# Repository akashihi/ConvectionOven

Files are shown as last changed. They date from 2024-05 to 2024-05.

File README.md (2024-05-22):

<!-- Improved compatibility of back to top link: See: https://github.com/othneildrew/Best-README-Template/pull/73 -->

<h3 align="center">Adler Ad 6304 Convection Oven controller board</h3>
<div>
  <p align="center">
    Modern replacement for the Adler Ad 6304 control circuit. 
    <br />
    <a href="https://github.com/akashihi/ConvectionOven"><strong>Explore the docs »</strong></a>
    <br />
    <br />
  </p>
</div>

<!-- TABLE OF CONTENTS -->
<details>
  <summary>Table of Contents</summary>
  <ol>
    <li>
      <a href="#about-the-project">About The Project</a>
    </li>
    <li>
      <a href="#getting-started">Getting Started</a>
      <ul>
        <li><a href="#housing">Housing</a></li>
        <li><a href="#controls">Controls</a></li>
        <li><a href="#hall-sensor">Hall sensor</a></li>
        <li><a href="#pcb">PCB</a></li>
        <li><a href="#firmware">Firmware</a></li>
      </ul>
    </li>
    <li><a href="#usage">Usage</a></li>
    <li><a href="#roadmap">Roadmap</a></li>
    <li><a href="#contributing">Contributing</a></li>
    <li><a href="#license">License</a></li>
    <li><a href="#contact">Contact</a></li>
  </ol>
</details>

<!-- ABOUT THE PROJECT -->
## About The Project

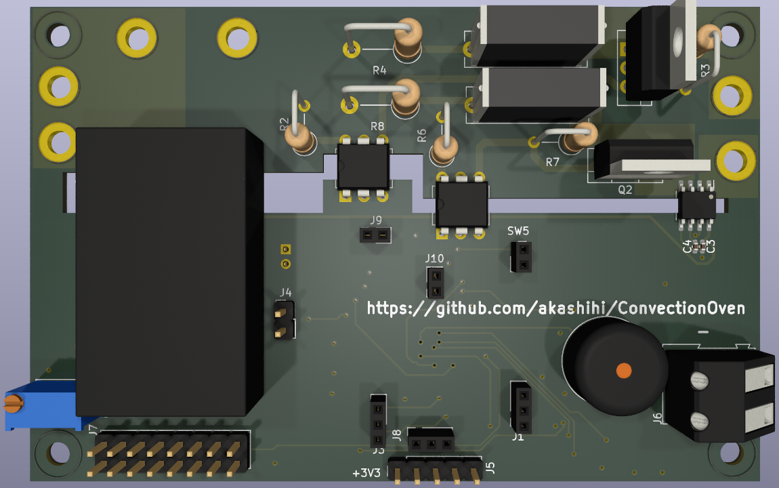
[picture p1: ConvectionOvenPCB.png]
Product Name Screen Shot


This is a drop-in replacement of an analog control circuit of the Adler Ad 6304 oven.

The updated control circuit provides the following improvements to the original circuit:

* Easily cancellable timer
* Magnetic handle position sensor
* PID temperature control
* LCD user interface
* Overheat protection
* Motor protection (currently disabled in firmware)
* Sleeping mode (currently disabled)

<p align="right">(<a href="#readme-top">back to top</a>)</p>

<!-- GETTING STARTED -->
## Getting Started

Get an Adler Ad 6304 oven that you would like to upgrade. Broken oven is fine too, 
in case heater element and motor are still working. You will need to completely disassemble
the oven and remove most of it. However, some elements will be reused:

* Heater and heater wires
* Motor and motor wires
* Thermistor. It is hidden in the white braid and mounted directly to the upper fan housing. 
Leave it as it is or move closer to the power outlet.

Everything else, including the plastic enclosure, could be thrown to the trash :D 

### Housing

Housing consists of five 3D printable parts:

* Inner and outer axles
* Upper and lower handle parts
* The actual electronics housing

Both axles and handle parts are easy to print. The housing is more tricky, as you need 
supports only for the bigger overhands, like encoders insets or cut for a handle. 
You *do not* need supports for the ventilation cuts. Putting supports there will make your life
much harder, as those supports are almost impossible to remove.

While assembling the housing, you need to put inner axles through the housing and glue them
to the outer axles, so they will become a real axle. For the handle you'll need some M3 bolts
and nuts. Additionally, you need to put several strong 6mmx3mm magnets into the magnet
pocket of the lower handle.

After assembling the handle, put the M3 insets into the hall sensor PCB mounting holes,
screen mounting holes and the main PCB mounting holes.

As the last step, mount the IEC 60320 C14 connector to the respective slot on the housing side.

<p align="right">(<a href="#readme-top">back to top</a>)</p>

### Controls

All controls are mounted to the housing. You will need to mount:

* Two encoders, one for the temperature setting, one for the timer setting
* Two buttons. One for the sleep mode (unused atm), one to switch the cooking mode on and off
* Two LEDs, one shows whether oven is cooking or not, another one shows the heater state
* 16x2 HD44780 screen with 3.3V support. The 5V screens will not work in this design.

<p align="right">(<a href="#readme-top">back to top</a>)</p>

### Hall sensor

Hall sensor is mounted on a separate PCB under the handle. This design uses omni-polar
hall sensor with an open-drain output.

<p align="right">(<a href="#readme-top">back to top</a>)</p>

### PCB

Control PCB is a four layer PCB, split into hot side and cold side. Follow the schematics
and PCB design for the assembly. Additional guidance:

* The U3 IC is required, as it closes the motor control circuit. However, it is not
used in the firmware, so rest of the components (C3, C4, R11, R12, D1, C20) could be omitted for now.
* You can skip the U4 IC and related components (R10, C11, C6, C5)
* You need to short circuit R25, as there is no sleep mode implemented yet
* TRIACs Q1 and Q2 *require* heatsinks
* You may test the cold side of the circuit by injecting power (+5V) directly to the J4

Assembled PCB should be put into the housing and connected to the controls, power socket, heater and
motor. Please connect motor to the control channel equipped with a current sensor. It
is recommended to have a fuse between the power socket and the control PCB. Same way
connect the thermistor, mentioned above, in series with the fuse.

<p align="right">(<a href="#readme-top">back to top</a>)</p>

### Firmware

Precompiled firmware is provided in the `fw.bin` file. 

The firmware is written in Rust and could be compiled with the following commands:

```shell
cargo build --release
cargo objcopy --release --bin fw -- -O binary fw.bin
```

You can upload the firmware with a `st-flash` tool:

```shell
st-flash erase 
st-flash write fw.hex 0x8000000
st-flash reset
```

The oven should start immediately after reset

<p align="right">(<a href="#readme-top">back to top</a>)</p>

## Usage

To start cooking you have to set a timer (up to 3 hours) and desired temperature (up to 250 degrees),
lower the handle and press cooking button. The oven will start immediately.

Raising the handle or pressing the cooking button stops the motor and heater instantly.

You can adjust the timer and desired temperature during the cooking. In one minute before
the timer expiration you will get a short beep accompanied by a longer beep after timer
expiration.

After cooking please immediately open the oven and put a top lid on the lid rack to 
avoid circuit overheat.  

<p align="right">(<a href="#readme-top">back to top</a>)</p>

<!-- ROADMAP -->
## Roadmap

- [ ] Implement sleep mode
- [ ] Implement motor protection

<p align="right">(<a href="#readme-top">back to top</a>)</p>

<!-- CONTRIBUTING -->
## Contributing

Contributions are what make the open source community such an amazing place to learn, inspire, and create. Any contributions you make are **greatly appreciated**.

If you have a suggestion that would make this better, please fork the repo and create a pull request.

1. Fork the Project
2. Create your Feature Branch (`git checkout -b feature/AmazingFeature`)
3. Commit your Changes (`git commit -m 'Add some AmazingFeature'`)
4. Push to the Branch (`git push origin feature/AmazingFeature`)
5. Open a Pull Request

<p align="right">(<a href="#readme-top">back to top</a>)</p>

<!-- LICENSE -->
## License

Distributed under the GPLv3 License. See `LICENSE.txt` for more information.

<p align="right">(<a href="#readme-top">back to top</a>)</p>

<!-- CONTACT -->
## Contact

Denis Chaplygin - @akashihi@mathstodon.xyz - akashihi@gmail.com

Project Link: [https://github.com/akashihi/ConvectionOven](https://github.com/github_username/repo_name)

<p align="right">(<a href="#readme-top">back to top</a>)</p>

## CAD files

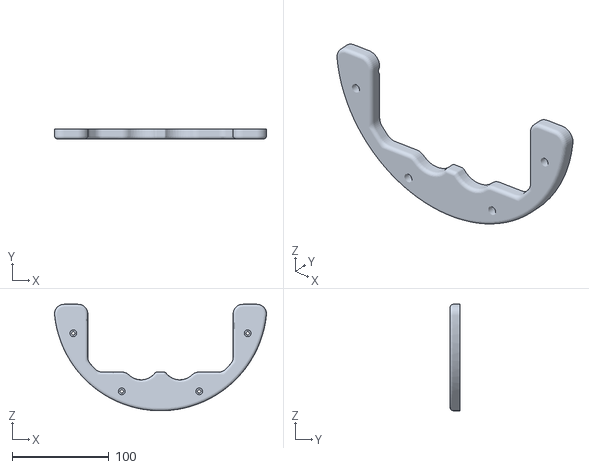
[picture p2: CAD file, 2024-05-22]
Housing/UpperHandle.STL
219.0 x 10.00 x 110.0

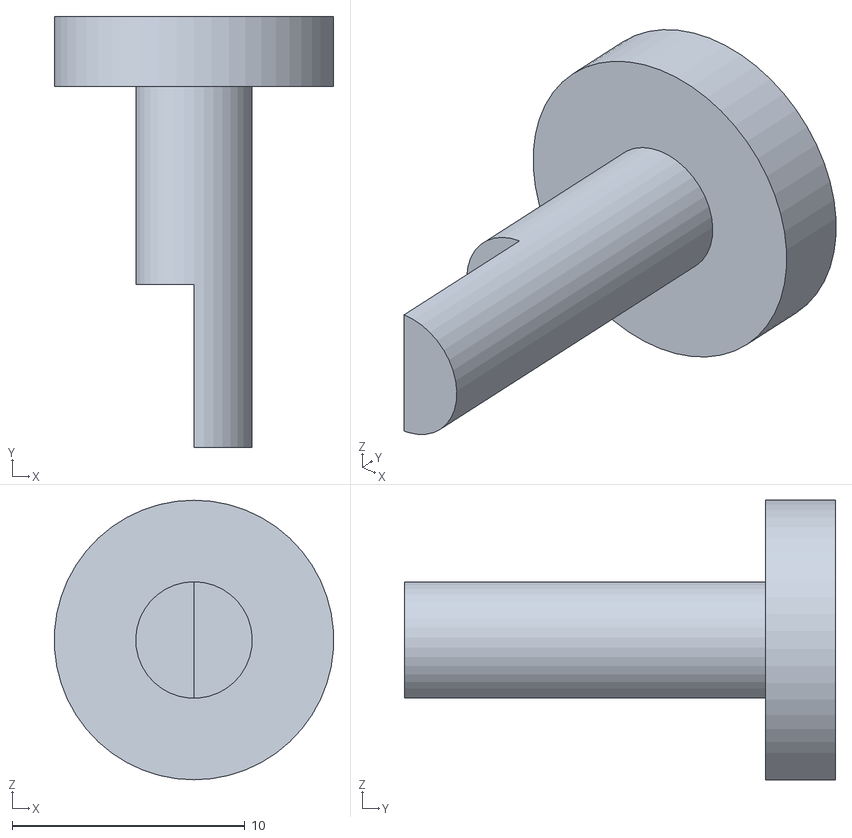
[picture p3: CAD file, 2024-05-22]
Housing/InnerAxle.STL
12.0 x 18.5 x 12.0

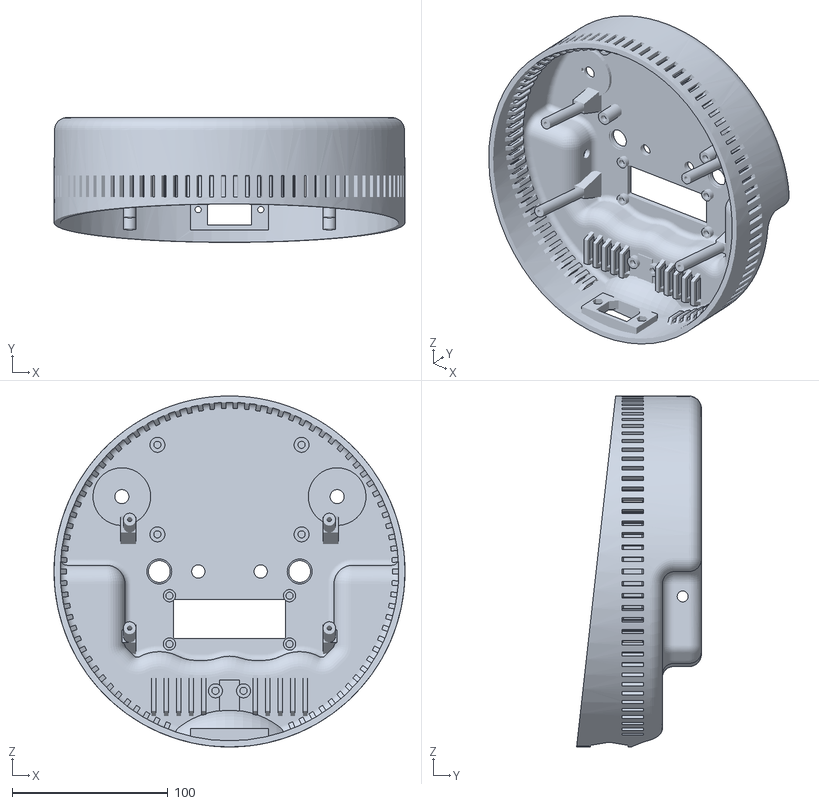
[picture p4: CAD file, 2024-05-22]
Housing/Cover.STL
225.0 x 80.0 x 225.0

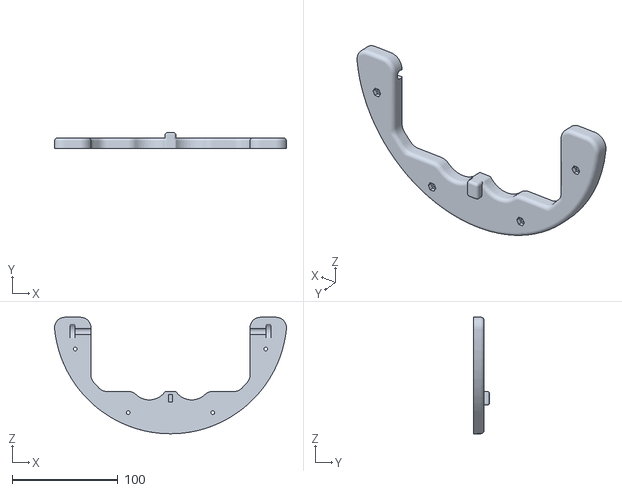
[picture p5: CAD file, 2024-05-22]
Housing/LowerHandle.STL
219.0 x 15.0 x 110.0

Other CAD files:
Housing/OuterAxle.STL

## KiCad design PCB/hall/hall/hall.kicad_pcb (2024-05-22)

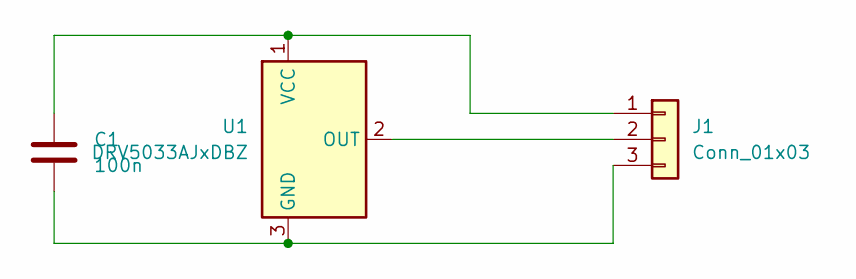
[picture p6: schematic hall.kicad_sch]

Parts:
C1: 100n; C_0603_1608Metric
J1: Conn_01x03; PinHeader_1x03_P2.00mm_Vertical
U1: DRV5033AJxDBZ; SOT-23

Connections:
unnamed: C1.1, J1.1, U1.1 (VCC)
unnamed: J1.2, U1.2 (OUT)
unnamed: C1.2, J1.3, U1.3 (GND)

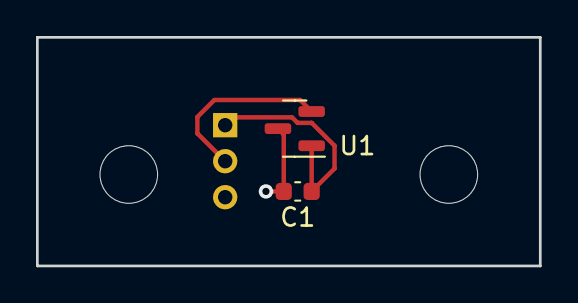
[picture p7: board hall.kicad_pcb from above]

Board: 2 copper layers, 27.9 x 12.7 mm, 3 parts (1 on the bottom side), 3 nets.

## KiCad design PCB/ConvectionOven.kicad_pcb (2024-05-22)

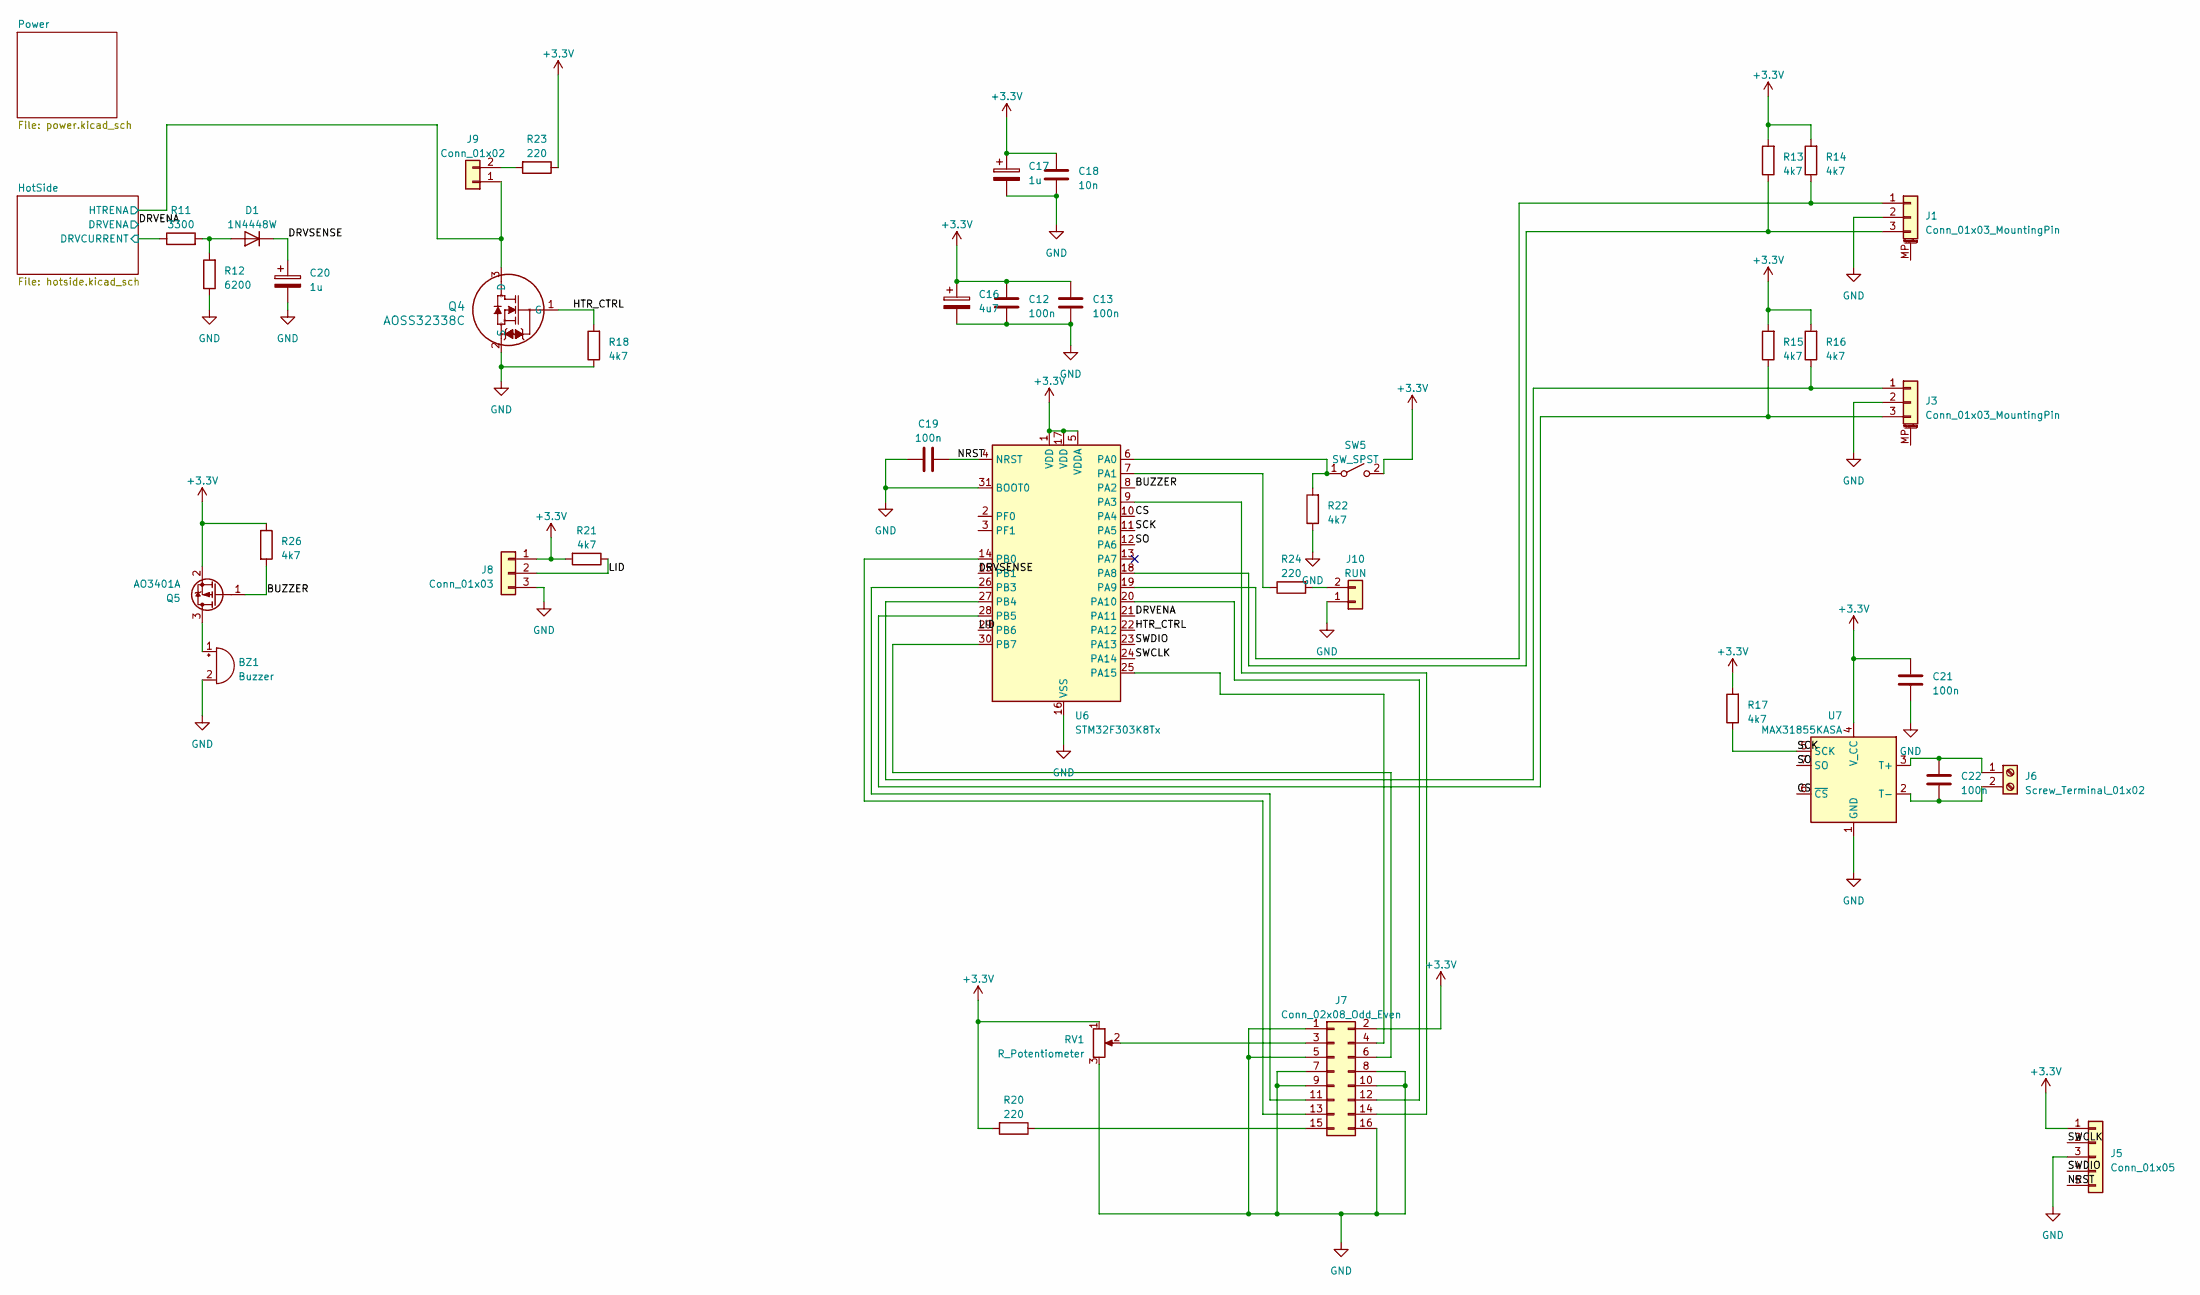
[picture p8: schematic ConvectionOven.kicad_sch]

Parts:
BZ1: Buzzer; Buzzer_12x9.5RM7.6
C12, C13, C19, C21, C22: 100n; C_0402_1005Metric_Pad0.74x0.62mm_HandSolder
C16: 4u7; C_Elec_4x5.4
C17, C20: 1u; C_0805_2012Metric_Pad1.18x1.45mm_HandSolder
C18: 10n; C_0805_2012Metric_Pad1.18x1.45mm_HandSolder
D1: 1N4448W; D_SOD-123
J1, J3: Conn_01x03_MountingPin; PinSocket_1x03_P2.00mm_Vertical
J5: Conn_01x05; PinHeader_1x05_P2.54mm_Vertical
J6: Screw_Terminal_01x02; TerminalBlock_Altech_AK300-2_P5.00mm
J7: Conn_02x08_Odd_Even; PinHeader_2x08_P2.54mm_Vertical
J8: Conn_01x03; PinSocket_1x03_P2.00mm_Vertical
J9: Conn_01x02; PinSocket_1x02_P2.00mm_Vertical
J10: RUN; PinSocket_1x02_P2.00mm_Vertical
Q4: AOSS32338C; SOT-23-3
Q5: AO3401A; SOT-23
R11: 3300; R_0805_2012Metric_Pad1.20x1.40mm_HandSolder
R12: 6200; R_1206_3216Metric_Pad1.30x1.75mm_HandSolder
R13, R14, R15, R16, R17, R18, R21, R22, R26: 4k7; R_0805_2012Metric_Pad1.20x1.40mm_HandSolder
R20, R23, R24: 220; R_0805_2012Metric_Pad1.20x1.40mm_HandSolder
RV1: R_Potentiometer; Potentiometer_Bourns_3296W_Vertical
SW5: SW_SPST; PinSocket_1x02_P2.00mm_Vertical
U6: STM32F303K8Tx; LQFP-32_7x7mm_P0.8mm
U7: MAX31855KASA; SOIC-8_3.9x4.9mm_P1.27mm

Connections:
+3.3V: C12.1, C13.1, C16.1, C17.1, C18.1, C21.1, J5.1, J7.2, J8.1, Q5.2 (S), R13.2, R14.2, R15.2, R16.2, R17.2, R20.2, R21.2, R23.1, R26.1, RV1.1, SW5.2 (B), U6.1 (VDD), U6.5 (VDDA), U6.17 (VDD), U7.4 (V_CC); also elsewhere on the board
/BUZZER: Q5.1 (G), R26.2, U6.8 (PA2)
/CS: U6.10 (PA4), U7.6 (~CS)
/DRVENA: U6.21 (PA11); also elsewhere on the board
/DRVSENSE: C20.1, D1.1 (K), U6.15 (PB1)
/HTR_CTRL: Q4.1 (G), R18.2, U6.22 (PA12)
/HotSide/DRVCURRENT: R11.1; also elsewhere on the board
/HotSide/HTRENA: J9.1, Q4.3 (D); also elsewhere on the board
/LID: J8.2, R21.1, U6.29 (PB6)
/NRST: C19.2, J5.5, U6.4 (NRST)
/SCK: R17.1, U6.11 (PA5), U7.5 (SCK)
/SO: U6.12 (PA6), U7.7 (SO)
/SWCLK: J5.2, U6.24 (PA14)
/SWDIO: J5.4, U6.23 (PA13)
GND: BZ1.2 (+), C12.2, C13.2, C16.2, C17.2, C18.2, C19.1, C20.2, C21.2, J1.2, J3.2, J5.3, J7.1, J7.5, J7.7, J7.8, J7.9, J7.10, J7.16, J8.3, J10.1, Q4.2 (S), R12.1, R18.1, R22.1, RV1.3, U6.16 (VSS), U6.31 (BOOT0), U6.32 (VSS), U7.1 (GND); also elsewhere on the board
unnamed: BZ1.1 (-), Q5.3 (D)
unnamed: D1.2 (A), R11.2, R12.2
unnamed: J1.1, R14.1, U6.19 (PA9)
unnamed: J1.3, R13.1, U6.18 (PA8)
unnamed: J3.1, R16.1, U6.27 (PB4)
unnamed: J3.3, R15.1, U6.28 (PB5)
unnamed: C22.1, J6.1, U7.3 (T+)
unnamed: C22.2, J6.2, U7.2 (T-)
unnamed: J7.3, RV1.2
unnamed: J7.4, U6.25 (PA15)
unnamed: J7.6, U6.30 (PB7)
unnamed: J7.11, U6.26 (PB3)
unnamed: J7.12, U6.20 (PA10)
unnamed: J7.13, U6.14 (PB0)
unnamed: J7.14, U6.9 (PA3)
unnamed: J7.15, R20.1
unnamed: J9.2, R23.2
unnamed: J10.2, R24.2
unnamed: R22.2, SW5.1 (A), U6.6 (PA0)
unnamed: R24.1, U6.7 (PA1)

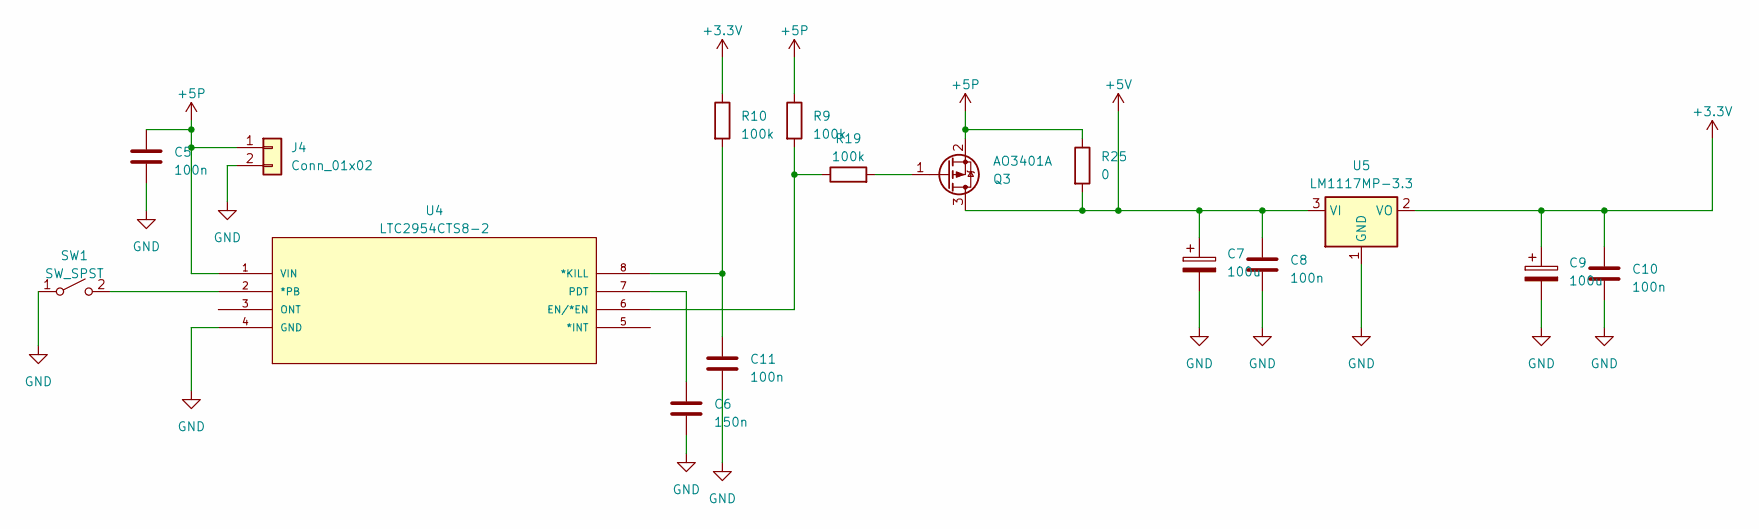
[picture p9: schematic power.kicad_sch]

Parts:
C5, C8, C10, C11: 100n; C_0402_1005Metric_Pad0.74x0.62mm_HandSolder
C6: 150n; C_0402_1005Metric_Pad0.74x0.62mm_HandSolder
C7, C9: 100u; CP_EIA-7343-15_Kemet-W_Pad2.25x2.55mm_HandSolder
J4: Conn_01x02; PinHeader_1x02_P2.54mm_Vertical
Q3: AO3401A; SOT-23
R9, R19: 100k; R_0805_2012Metric_Pad1.20x1.40mm_HandSolder
R10: 100k; R_0603_1608Metric_Pad0.98x0.95mm_HandSolder
R25: 0; R_0805_2012Metric_Pad1.20x1.40mm_HandSolder
SW1: SW_SPST; PinSocket_1x02_P2.00mm_Vertical
U4: LTC2954CTS8-2; TSOT-23-8_HandSoldering; MANUFACTURER_PART_NUMBER ltc2954cts82
U5: LM1117MP-3.3; SOT-223-3_TabPin2

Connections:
+3.3V: C9.1, C10.1, R10.1, U5.2 (VO); also elsewhere on the board
+5P: C5.1, J4.1, Q3.2 (S), R9.1, R25.1, U4.1 (VIN); also elsewhere on the board
+5V: C7.1, C8.1, Q3.3 (D), R25.2, U5.3 (VI); also elsewhere on the board
GND: C5.2, C6.2, C7.2, C8.2, C9.2, C10.2, C11.2, J4.2, SW1.1 (A), U4.4 (GND), U5.1 (GND); also elsewhere on the board
unnamed: Q3.1 (G), R19.2
unnamed: SW1.2 (B), U4.2 (*PB)
unnamed: C11.1, R10.2, U4.8 (*KILL)
unnamed: R9.2, R19.1, U4.6 (EN/*EN)
unnamed: C6.1, U4.7 (PDT)

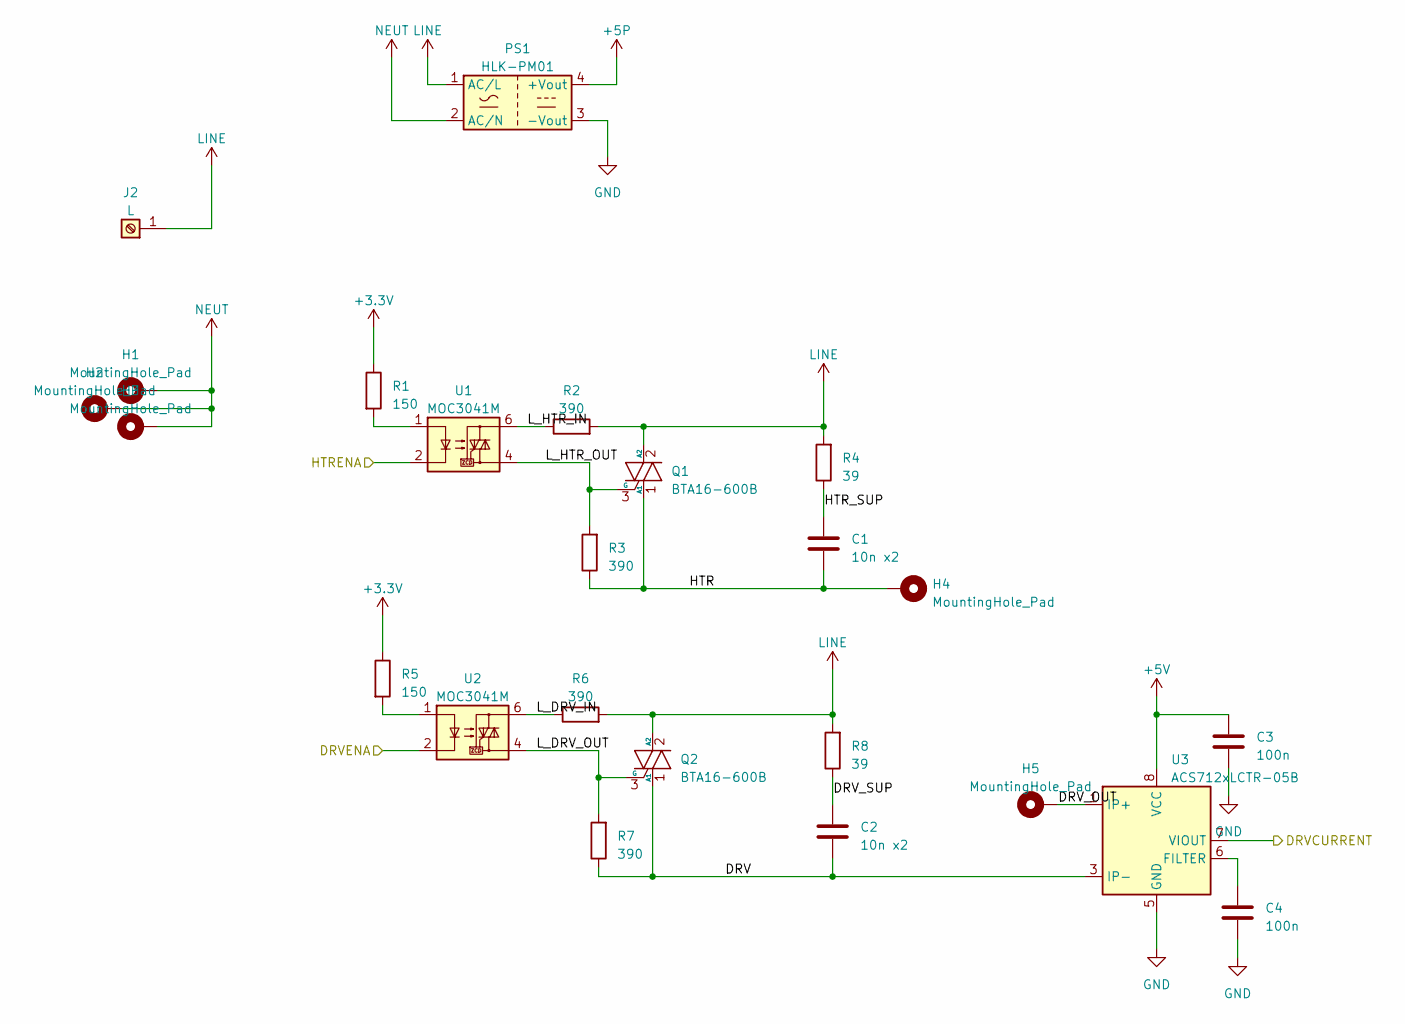
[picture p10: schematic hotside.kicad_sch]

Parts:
C1, C2: 10n x2; C_Rect_L16.5mm_W4.7mm_P15.00mm_MKT
C3, C4: 100n; C_0402_1005Metric_Pad0.74x0.62mm_HandSolder
H1, H2, H3, H4, H5: MountingHole_Pad; MountingHole_3.2mm_M3_DIN965_Pad_TopBottom
J2: L; MountingHole_3.2mm_M3_DIN965_Pad_TopBottom
PS1: HLK-PM01; Converter_ACDC_HiLink_HLK-PMxx
Q1, Q2: BTA16-600B; TO-220-3_Vertical
R1, R5: 150; R_0603_1608Metric_Pad0.98x0.95mm_HandSolder
R2, R3, R6, R7: 390; R_Axial_DIN0309_L9.0mm_D3.2mm_P5.08mm_Vertical
R4, R8: 39; R_Axial_DIN0411_L9.9mm_D3.6mm_P7.62mm_Vertical
U1, U2: MOC3041M; DIP-6_W7.62mm
U3: ACS712xLCTR-05B; SOIC-8_3.9x4.9mm_P1.27mm

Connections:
+3.3V: R1.1, R5.1; also elsewhere on the board
+5P: PS1.4 (+Vout); also elsewhere on the board
+5V: C3.1, U3.8 (VCC); also elsewhere on the board
/DRVENA: U2.2; also elsewhere on the board
/HotSide/DRV: C2.2, Q2.1 (A1), R7.1, U3.3 (IP-), U3.4 (IP-)
/HotSide/DRVCURRENT: U3.7 (VIOUT); also elsewhere on the board
/HotSide/DRV_OUT: H5.1, U3.1 (IP+), U3.2 (IP+)
/HotSide/DRV_SUP: C2.1, R8.1
/HotSide/HTR: C1.2, H4.1, Q1.1 (A1), R3.1
/HotSide/HTRENA: U1.2; also elsewhere on the board
/HotSide/HTR_SUP: C1.1, R4.1
/HotSide/L_DRV_IN: R6.1, U2.6
/HotSide/L_DRV_OUT: Q2.3 (G), R7.2, U2.4
/HotSide/L_HTR_IN: R2.1, U1.6
/HotSide/L_HTR_OUT: Q1.3 (G), R3.2, U1.4
GND: C3.2, C4.2, PS1.3 (-Vout), U3.5 (GND); also elsewhere on the board
LINE: J2.1, PS1.1 (AC/L), Q1.2 (A2), Q2.2 (A2), R2.2, R4.2, R6.2, R8.2
NEUT: H1.1, H2.1, H3.1, PS1.2 (AC/N)
unnamed: R1.2, U1.1
unnamed: R5.2, U2.1
unnamed: C4.1, U3.6 (FILTER)

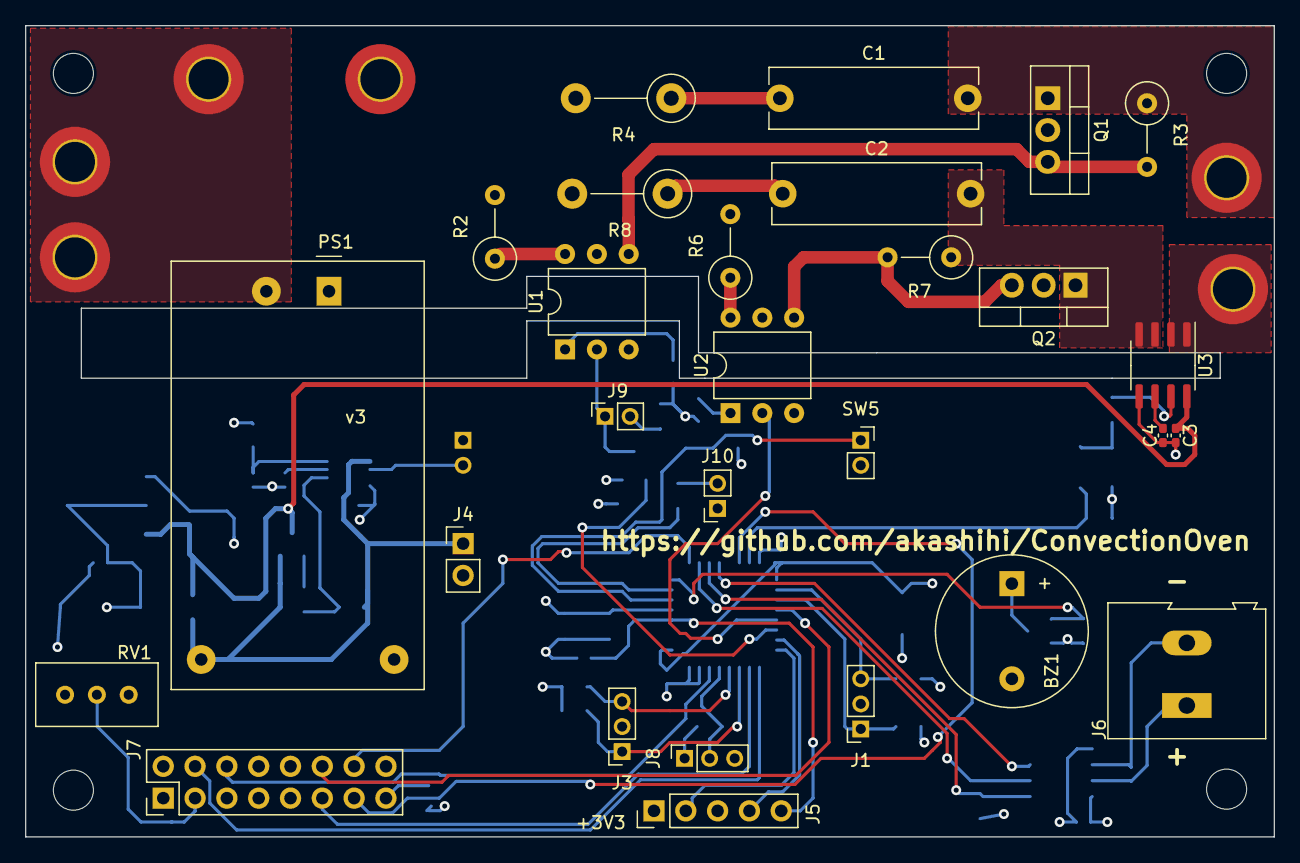
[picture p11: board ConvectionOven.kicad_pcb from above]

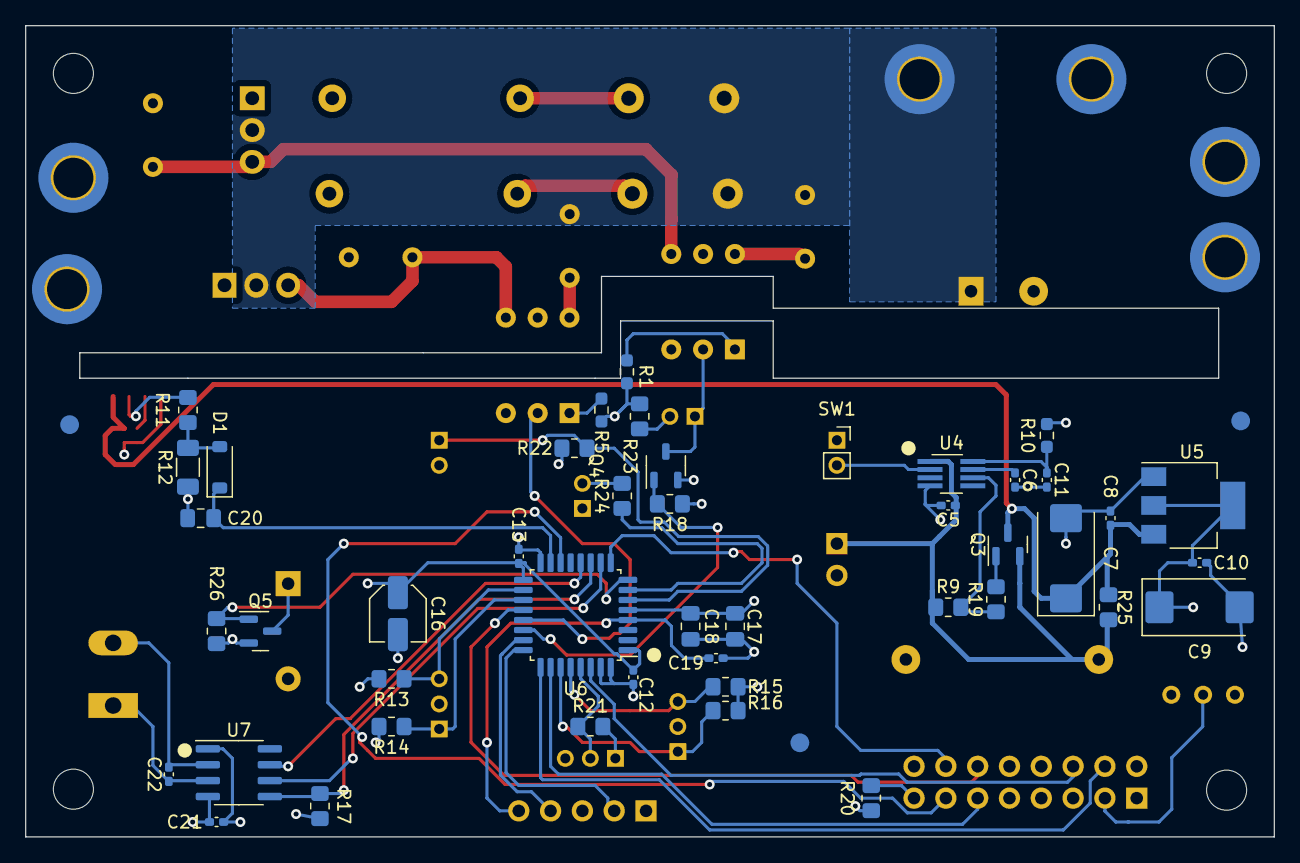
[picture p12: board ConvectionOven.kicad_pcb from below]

Board: 4 copper layers, 99.7 x 64.8 mm, 79 parts (45 on the bottom side), 56 nets.

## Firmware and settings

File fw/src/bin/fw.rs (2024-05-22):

#![no_main]
#![no_std]

extern crate panic_halt;

use fw as _;

#[rtic::app(device = stm32f3xx_hal::pac, dispatchers = [FMC])]
mod app {
    use cortex_m::peripheral::NVIC;
    use stm32f3xx_hal::prelude::*;
    use dwt_systick_monotonic::DwtSystick;
    use stm32f3xx_hal::gpio::Edge;
    use stm32f3xx_hal::timer::{Timer, Event};
    use stm32f3xx_hal::adc;
    use fw::board::{Board, CookBtn, Lid};
    use fw::encoder::{EncoderReaderTIM1, EncoderReaderTIM3};
    use dwt_systick_monotonic::ExtU32;
    use stm32f3xx_hal::adc::{VoltageInternalReference};
    use stm32f3xx_hal::pac::{TIM2, TIM6, TIM15};
    use fw::buzzer::BuzzerManager;
    use fw::current_sensor::{CurrentReader, CurrentSensor};
    use fw::delay::TimDelay;
    use fw::display::LcdDisplay;
    use fw::state::manager::StateManager;
    use fw::state::OvenControlHardware;
    use fw::temp_sensor::TempSensor;

    #[monotonic(binds = SysTick, default = true)]
    type SysMono = DwtSystick<64_000_000>;

    #[shared]
    struct Shared {
        cook_btn_debounce: bool,
        lid_debounce: bool,
        lid: Lid,
        state: StateManager,
    }

    #[local]
    struct Local {
        cook_btn: CookBtn,
        current_timer: Timer<TIM2>,
        current_reader: CurrentReader,
        state_poll_timer: Timer<TIM6>,
        pid_timer: Timer<TIM15>
    }

    #[init]
    fn init(mut cx: init::Context) -> (Shared, Local, init::Monotonics) {
        //Set up the system clock
        let mut rcc = cx.device.RCC.constrain();
        let mut flash = cx.device.FLASH.constrain();
        let clocks = rcc.cfgr.sysclk(64.MHz()).freeze(&mut flash.acr);
        let mut syscfg = cx.device.SYSCFG.constrain(&mut rcc.apb2);
        let mut exti = cx.device.EXTI;

        //Set up monotonic timer
        cx.core.DCB.enable_trace();
        cx.core.DWT.enable_cycle_counter();
        let mono = DwtSystick::new(&mut cx.core.DCB, cx.core.DWT, cx.core.SYST, clocks.hclk().0);

        //Configure TIM7 as a delay provider
        let mut delay = TimDelay::new(cx.device.TIM7, clocks, &mut rcc.apb1);

        //Configure board
        let mut board = Board::new(cx.device.GPIOA, cx.device.GPIOB, cx.device.SPI1, &mut rcc.ahb, &mut rcc.apb2, clocks, &mut delay);

        //Setup event timers
        let mut state_poll_timer = Timer::new(cx.device.TIM6, clocks, &mut rcc.apb1);
        state_poll_timer.start(100.milliseconds());
        state_poll_timer.enable_interrupt(Event::Update);
        let mut pid_timer = Timer::new(cx.device.TIM15, clocks, &mut rcc.apb2);
        pid_timer.start(10.seconds());
        pid_timer.enable_interrupt(Event::Update);

        //Configure temperature encoder
        let tim1 = Timer::new(cx.device.TIM1, clocks, &mut rcc.apb2);
        let temp_encoder = EncoderReaderTIM1::new(tim1.free(), 10, 50);

        //Configure time encoder
        let tim3 = Timer::new(cx.device.TIM3, clocks, &mut rcc.apb1);
        let time_encoder = EncoderReaderTIM3::new(tim3.free(), 0, 180);

        //Configure drive current sensor
        let mut current_timer = Timer::new(cx.device.TIM2, clocks, &mut rcc.apb1);
        current_timer.start(10.milliseconds());
        current_timer.enable_interrupt(Event::Update);
        let mut adc_common_current = adc::CommonAdc::new(cx.device.ADC1_2, &clocks, &mut rcc.ahb);
        let mut adc_pair_current = (cx.device.ADC1, cx.device.ADC2);
        let v_in = VoltageInternalReference::new(&mut adc_common_current, &mut adc_pair_current);
        let adc_current = adc::Adc::new(adc_pair_current.0, adc::config::Config::default(), &clocks, &adc_common_current).into_oneshot();

        //Configure the interrrupts
        syscfg.select_exti_interrupt_source(&board.cook_btn);
        board.cook_btn.trigger_on_edge(&mut exti, Edge::Rising);
        board.cook_btn.enable_interrupt(&mut exti);
        syscfg.select_exti_interrupt_source(&board.lid);
        board.lid.trigger_on_edge(&mut exti, Edge::Falling);
        board.lid.enable_interrupt(&mut exti);

        unsafe {
            NVIC::unmask(board.cook_btn.interrupt());
            NVIC::unmask(board.lid.interrupt());
            NVIC::unmask(current_timer.interrupt());
            NVIC::unmask(state_poll_timer.interrupt());
            NVIC::unmask(pid_timer.interrupt());
        };

        //Configure control structs
        let display_manager = LcdDisplay::new(board.lcd, delay);
        let temp_sensor = TempSensor::new(board.tc_cs, board.tc_spi);
        let buzzer = BuzzerManager::new(board.buzzer);
        let current_reader = CurrentReader::new(adc_current, v_in, board.current);
        let current_sensor = CurrentSensor::new();
        let control_hardware = OvenControlHardware{display: display_manager, buzzer, cook_ld: board.cook_ld, heater: board.heater, motor: board.motor};
        let state_manager = StateManager::new(control_hardware, current_sensor, temp_encoder, time_encoder, temp_sensor);

        let shared = Shared {
            cook_btn_debounce: false,
            lid_debounce: false,
            lid: board.lid,
            state: state_manager
        };

        let local = Local {
            cook_btn: board.cook_btn,
            current_timer,
            current_reader,
            state_poll_timer,
            pid_timer
        };

        (shared, local, init::Monotonics(mono))
    }

    #[task(binds = TIM2, local = [current_timer, current_reader], shared=[state])]
    fn current_timer_handle(mut cx: current_timer_handle::Context) {
        // TODO ADC should be triggered by timer directly,
        // and use DMA to read both channels in sequence
        // but i'm lazy and it is fast enough to not to cause any issues
        cx.local.current_timer.clear_events();
        cx.shared.state.lock(|state| state.adc_poll(cx.local.current_reader.read()));
    }

    #[task(binds = EXTI0, local = [cook_btn], shared = [cook_btn_debounce,state])]
    fn cook_btn_handler(cx: cook_btn_handler::Context) {
        cx.local.cook_btn.clear_interrupt();
        let cook_btn_handler::SharedResources { mut cook_btn_debounce, mut state } = cx.shared;
        cook_btn_debounce.lock(|debounce|
            if !*debounce {
                *debounce = true;
                state.lock(|s| s.on_cook_btn());
                cook_btn_debounce::spawn_after(300.millis()).unwrap();
            }
        );
    }

    #[task(shared = [cook_btn_debounce])]
    fn cook_btn_debounce(mut cx: cook_btn_debounce::Context) {
        cx.shared.cook_btn_debounce.lock(|debounce| *debounce = false);
    }

    #[task(binds = EXTI9_5, shared = [lid, lid_debounce, state])]
    fn lid_handler(cx: lid_handler::Context) {
        let lid_handler::SharedResources { mut lid, mut lid_debounce, mut state } = cx.shared;
        lid.lock(|l| l.clear_interrupt());
        lid_debounce.lock(|debounce|
            if !*debounce {
                *debounce = true;
                state.lock(|s| s.enc_poll(false));
                lid_debounce::spawn_after(100.millis()).unwrap();
            }
        );
    }

    #[task(shared = [lid_debounce])]
    fn lid_debounce(mut cx: lid_debounce::Context) {
        cx.shared.lid_debounce.lock(|debounce| *debounce = false);
    }

    #[task(binds = TIM6_DACUNDER, local = [state_poll_timer], shared = [state, lid])]
    fn state_timer_handler(cx: state_timer_handler::Context) {
        cx.local.state_poll_timer.clear_events();
        let state_timer_handler::SharedResources { state, lid } = cx.shared;
        (state, lid).lock(|state, lid| {
            state.enc_poll(lid.is_low().unwrap_or(false));
        });
    }

    #[task(binds = TIM1_BRK_TIM15, local = [pid_timer], shared = [state])]
    fn pid_timer_handler(mut cx: pid_timer_handler::Context) {
        cx.local.pid_timer.clear_events();
        cx.shared.state.lock(|state| state.pid_poll())
    }
}

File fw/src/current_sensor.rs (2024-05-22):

use core::ptr;
use heapless::Deque;
use stm32f3xx_hal::adc::{Adc, OneShot, VoltageInternalReference};
use stm32f3xx_hal::pac::{ADC1, ADC1_2};
use stm32f3xx_hal::prelude::_embedded_hal_adc_OneShot;
use crate::board;

type ValuesRing = Deque<f32, 10>;

pub struct CurrentReader {
    adc_current: Adc<ADC1, OneShot>,
    v_in: VoltageInternalReference<ADC1_2>,
    current_pin: board::Current,
}

impl CurrentReader {
    pub fn new(adc_current: Adc<ADC1, OneShot>, v_in: VoltageInternalReference<ADC1_2>, current_pin: board::Current) -> Self {
        CurrentReader{adc_current, v_in, current_pin}
    }

    pub fn read(&mut self ) -> f32 {
        let value: u16 = self.adc_current.read(&mut self.current_pin).unwrap();
        let vref: u16 = self.adc_current.read(&mut self.v_in).unwrap();
        let vrefint_cal_ptr = 0x1FFF_F7BA as *const u16;
        let vrefint_cal = unsafe { ptr::read(vrefint_cal_ptr) };
        (3.3 * (vrefint_cal as f32) * (value as f32)) / (vref as f32 * 4095.0) // Convert to volts
    }
}

pub struct CurrentSensor {
    sensor_values: ValuesRing,
}

fn average(values: &ValuesRing) -> Option<f32>{
    if values.is_empty() || values.len() < 100 {
        None
    } else {
        Some(values.iter().sum::<f32>()/values.len() as f32)
    }
}

impl CurrentSensor {
    pub fn new() -> Self {
        CurrentSensor {sensor_values: Deque::new()}
    }

    pub fn add_value(&mut self, volts: f32) {
        if self.sensor_values.is_full() {
            self.sensor_values.pop_front();
        }
        if let Some(last_value) = self.sensor_values.front() {
            self.sensor_values.push_back((last_value*0.99) + (1.0-0.99)*volts).unwrap_or_default();
        } else {
            self.sensor_values.push_back(volts).unwrap_or_default();
        }
        //defmt::println!("Current averaged value: {}", self.sensor_values.iter().last().unwrap_or(&-1.0));
        /*let mut it = self.sensor_values.iter().rev();
        let last_value =  it.next().unwrap_or(&-1.0);
        let second_last_value =  it.next().unwrap_or(&-1.0);*/
        /*if last_value - second_last_value >= 0.002 {
            defmt::println!("Motor is on!")
        }
        if second_last_value - last_value >= 0.002 {
            defmt::println!("Motor is off!")
        }*/
    }

    pub fn get_sensor(&self) -> f32 {
        average(&self.sensor_values).unwrap_or(-1.0)
    }

    pub fn is_error(&self) -> bool {
        //average(&self.sensor_values).map(|v| v < 0.01).unwrap_or(false)
        false
    }

    pub fn is_standby(&self) -> bool {
        //defmt::println!("Idel value: {}, running value: {}", self.idle_current, average(&self.sensor_values));
        //average(&self.sensor_values).map(|v| fabsf(v - self.idle_current) < 0.001).unwrap_or(true)
        true
    }

    pub fn is_running(&self) -> bool {
        //defmt::println!("Idel value: {}, running value: {}", self.idle_current, average(&self.sensor_values));
        //average(&self.sensor_values).map(|v| fabsf(v - self.idle_current) < 0.005).unwrap_or(false)
        true
    }

    pub fn is_overloaded(&self) -> bool {
        //average(&self.sensor_values).map(|v| fabsf(v - self.idle_current)>0.1 && !self.is_error()).unwrap_or(false)
        false
    }

}

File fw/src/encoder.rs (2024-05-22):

use stm32f3xx_hal::pac::{TIM1, TIM3};
use paste::paste;
macro_rules! encoder_reader {
    ($timer:ident) => {
        paste! {
            pub struct [<EncoderReader $timer>] {
                enc: $timer,
                prev_value: u16,
                low_margin: u16,
                high_margin: u16
            }

            impl [<EncoderReader $timer>] {
                pub fn new(enc: $timer, low_margin: u16, high_margin: u16) -> Self {
                    //Configure timer to act as encoder interface
                    enc.smcr.modify(|_,w| w.sms().encoder_mode_1()); // Act on both channels
                    enc.ccer.modify(|_,w| w.cc1p().set_bit().cc2p().set_bit()); //On falling edge
                    enc.ccmr1_input().modify(|_, w| w.ic1f().fdts_div8_n6()); // Filter 8
                    let filter_value = enc.ccmr1_input().read().ic1f().bits();
                    enc.ccmr1_input().modify(|_, w| w.ic2f().bits(filter_value)); //Copy of filter 8
                    enc.ccmr1_input().modify(|_,w| w.cc1s().ti1().cc2s().ti2());
                    enc.psc.write(|w| w.psc().bits(0)); //No prescaler
                    enc.arr.write(|w| w.arr().bits(1024)); //1024 values
                    enc.cnt.write(|w| w.cnt().bits(512)); //Start in the middle
                    enc.cr1.modify(|_,w| w.cen().enabled()); //Start encoder interface

                    //Read the current value
                    let prev_value = enc.cnt.read().cnt().bits()>>1;
                    Self{enc, prev_value, low_margin, high_margin}
                }

                pub fn read(&mut self, current: u16) -> Option<u16> {
                    let dir = self.enc.cr1.read().dir().is_down();
                    let value = self.enc.cnt.read().cnt().bits() >> 1;
                    let steps = get_steps(dir, self.prev_value, value);
                    if steps != 0 {
                        self.prev_value = value;
                        let mut next_value = if dir {
                            current.saturating_sub(steps)
                        } else {
                            current + steps
                        };
                        // Clamping the range
                        if next_value < self.low_margin {
                            next_value = self.low_margin;
                        }
                        if next_value > self.high_margin {
                            next_value = self.high_margin;
                        }
                        Some(next_value)
                    } else {
                        None
                    }
                }
            }
        }
    }
}

encoder_reader!(TIM1);
encoder_reader!(TIM3);

fn get_steps(direction: bool, prev: u16, current: u16) -> u16 {
    if prev == current {
        return 0; //No changes
    }
    let steps = if direction { //Counting backwards
        if current > prev { //On backward count this means wrap
            512 - current + prev
        } else {
            prev - current
        }
    } else {
        if current < prev { //On forward count this means wrap
            512 - prev + current
        } else {
            current - prev
        }
    };
    if steps > 50 { //Most probably overspeed error, ignore it
        0
    } else {
        steps
    }
}
